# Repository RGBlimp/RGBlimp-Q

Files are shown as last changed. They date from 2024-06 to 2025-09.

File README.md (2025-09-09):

# RGBlimp-Q: Robotic Gliding Blimp With Moving Mass Control Based on a Bird-Inspired Continuum Arm
<div align="center">
    <a href="https://www.youtube.com/watch?v=U8VfF37lHvU" target="_blank">RGBlimp-Q</a>
</div>

These are the hardware and code for RGBlimp-Q. 

* [Project Page](https://RGBlimp.github.io)
* [Paper](https://arxiv.org/abs/2406.10810)
* [Video](https://youtu.be/U8VfF37lHvU)

# Demonstrations
### Robust Flight Against Wind
<div align="center">
    <br/>
    <br/>
    <br/>
</div>

### Attitude Adjustment
<div align="center">
    <br/>
    <br/>
</div>

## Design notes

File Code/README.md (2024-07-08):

# RGBlimp-Q Code

## ESP32-Arduino
ESP32 is a low-cost, low-power system on a chip microcontrollers with integrated Wi-Fi and dual-mode Bluetooth, which could be programmed through Arduino IDE. 

### Installing Arduino-ESP32 Support
Stable release link:
```
https://espressif.github.io/arduino-esp32/package_esp32_index.json
```
To start the installation process using the Boards Manager, follow these steps:
* Install the current upstream Arduino IDE at the 1.8 level or later. The current version is at the arduino.cc website.

* Start Arduino and open the Preferences window.

* Enter one of the release links above into Additional Board Manager URLs field. You can add multiple URLs, separating them with commas.

* Open Boards Manager from Tools > Board menu and install esp32 platform (and do not forget to select your ESP32 board from Tools > Board menu after installation).

* Restart Arduino IDE.

###### * See [Installing Guides](https://docs.espressif.com/projects/arduino-esp32/en/latest/installing.html) for more details on how to install the Arduino ESP32 support. 

### Installing Rosserial Arduino Library
Rosserial is a protocol for wrapping standard ROS serialized messages and multiplexing multiple topics and services over a character device such as a serial port or network socket. 
The rosserial arduino library support for Arduino compatible boards including ESP32. 

To install rosserial arduino library for Arduino IDE, follow these steps:
* Open the **Library Manager** from the IDE menu in Sketch -> Include Library -> Manage Library. 
* Search for "rosserial", and install. 

###### * See [Installing Guides](https://wiki.ros.org/rosserial_arduino/Tutorials/Arduino%20IDE%20Setup) for more details on how to install the rosserial arduino library for Arduino IDE. 

## ROS Package
This ROS package has been tested with ROS Melodic under Ubuntu 18.04. 
```
# Copy rgblimp_ros to catkin workspace

cd ~/catkin_ws/
catkin_make

source ~/catkin_ws/devel/setup.bash

roslaunch rgblimp_ros rgblimp_keyboard.launch
roslaunch rgblimp_ros rgblimp_tuner.launch
```

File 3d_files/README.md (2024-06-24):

# RGBlimp-Q Hardware 3D Files
### These files are derived from *Solidworks 2019 sp0*. 
<div align="center">
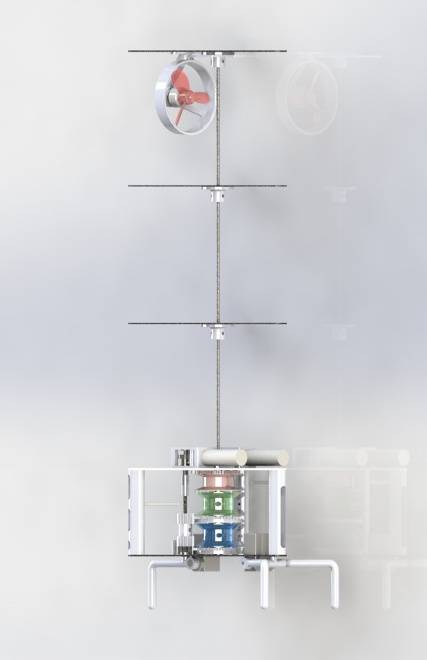
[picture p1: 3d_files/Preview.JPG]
    <br/>
    <sup>CAD Preview</sup><br/><br/>
</div>

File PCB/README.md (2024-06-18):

# RGBlimp-Q PCB

<div align="center">
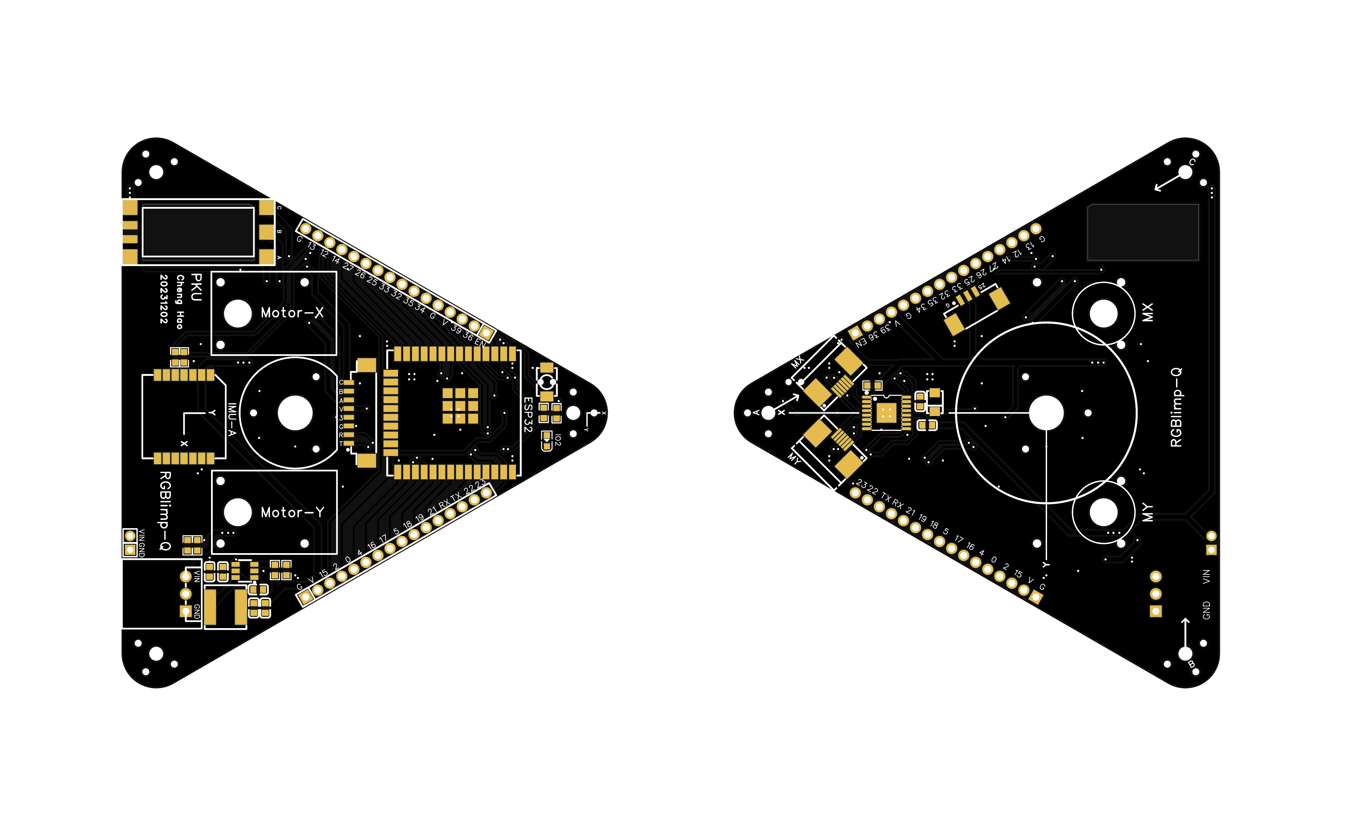
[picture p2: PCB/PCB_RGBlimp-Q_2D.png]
    <br/>
    <sup>Control Unit Circuit Board</sup><br/><br/>
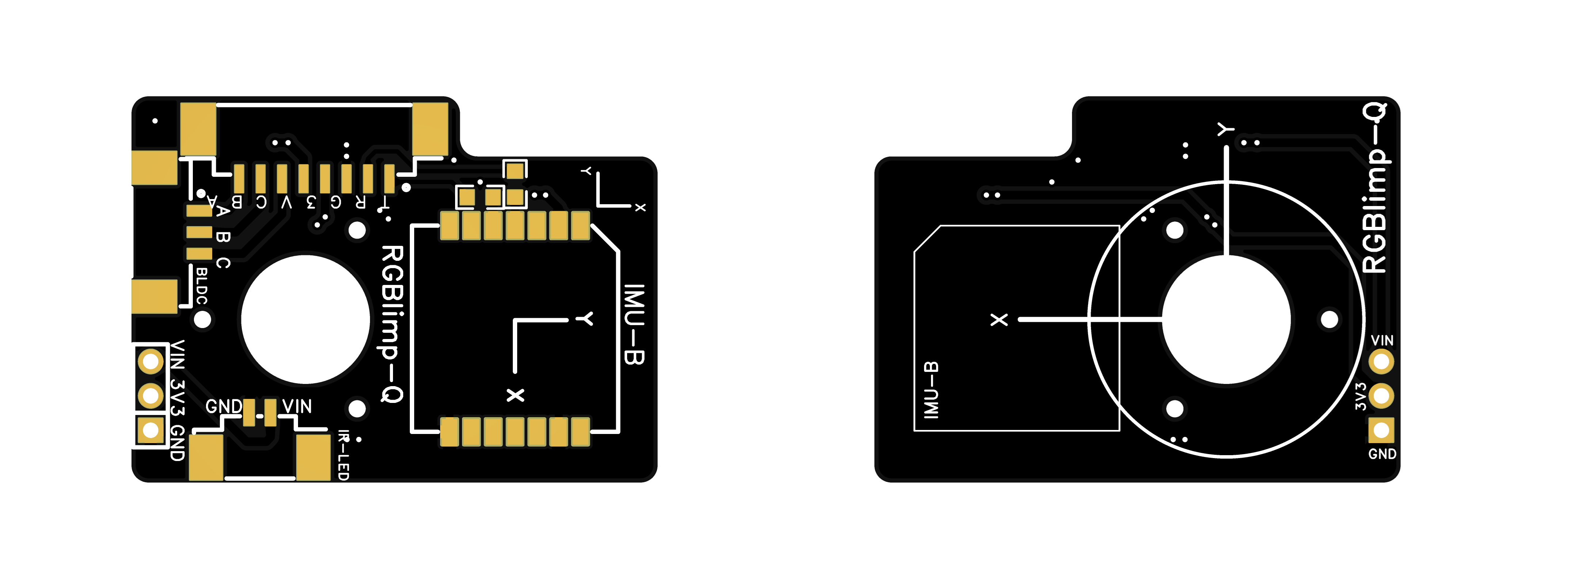
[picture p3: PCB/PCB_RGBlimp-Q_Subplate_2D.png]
    <br/>
    <sup>Subplate Circuit Board</sup>
</div>

## EasyEDA
The PCB project is also open-sourced on
[EasyEDA](https://oshwlab.com/ericccc413/rgblimp-q_)

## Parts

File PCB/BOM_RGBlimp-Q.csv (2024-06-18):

No. | Quantity | Comment | Designator(Main) | Footprint | Value | Manufacturer Part | Manufacturer | Supplier Part | Supplier
1 | 2 | 22uF | C1,C3 | C0603 |  | CL10A226MQ8NRNC | SAMSUNG | C59461 | LCSC
2 | 2 | 100nF | C2,C4 | C0603 |  | CC0603KRX7R9BB104 | YAGEO | C14663 | LCSC
3 | 1 | 22nF | C5 | C0603 |  | 0603B223K500NT | FH | C77571 | LCSC
4 | 1 | 10uF | C6 | CAP-SMD_L3.2-W1.6 |  | CA45-A-16V-10μF-K | TORCH | C185774 | LCSC
5 | 1 | 10nF | C7 | C0603 |  | GRM188R71H103KA01D | muRata | C77053 | LCSC
6 | 1 | 2.2uF | C8 | C0603 |  | CL10A225KO8NNNC | SAMSUNG | C23630 | LCSC
7 | 1 | S3B-XH-A (LF)(SN) | CN0 | CONN-TH_S3B-XH-A-LF-SN-RGBLIMP |  | S3B-XH-A(LF)(SN) | JST | C157928 | LCSC
9 | 1 | AFC12-S08CCC-00 | CN3 | CONN-SMD_8P-P1.25-V-M_AFC12-S08CCC-00 |  | AFC12-S08CCC-00 | JS | C395349 | LCSC
10 | 1 | AFC12-S03CCC-00 | CN4 | CONN-SMD_AFC12-S03CCC-00 |  | AFC12-S03CCC-00 | JS | C395344 | LCSC
11 | 1 | ESP32-WROOM-32UE(16MB) | ESP32 | WIFI-SMD_ESP32-WROOM-32UE |  | ESP32-WROOM-32UE-N16 | ESPRESSIF | C701346 | LCSC
13 | 1 | HI229 | IMU-A | HI229
14 | 1 | 10uH | L1 | IND-SMD_L6.0-W6.0_SWPA6045S |  | SWPA6045S100MT | Sunlord | C79272 | LCSC
15 | 1 | FC-DA1608BK-470H10 | LED1 | LED0603-RD |  | NCD0603B1 |  | C84266 | LCSC
16 | 2 | KH-FG0.5-H2.0-6PIN | MX,MY | FPC-SMD_KH-FG0.5-H2.0-6PIN |  | KH-FG0.5-H2.0-6PIN | Shenzhen Kinghelm Elec | C709363 | LCSC
17 | 1 | 68kΩ | R1 | R0603 |  | 0603WAF6802T5E | UNI-ROYAL | C23231 | LCSC
18 | 1 | 15kΩ | R2 | R0603 |  | 0603WAF1502T5E | UNI-ROYAL | C22809 | LCSC
19 | 2 | 10kΩ | R3,R6 | R0603 |  | 0603WAF1002T5E | UNI-ROYAL | C25804 | LCSC
20 | 1 | 20kΩ | R4 | R0603 |  | 0603WAF2002T5E | UNI-ROYAL | C4184 | LCSC
21 | 1 | 1kΩ | R5 | R0603 |  | 0603WAF1001T5E | UNI-ROYAL | C21190 | LCSC
22 | 1 | 47kΩ | R7 | R0603 |  | 0603WAF4702T5E | UNI-ROYAL | C25819 | LCSC
23 | 2 | 120Ω | R8,R9 | R0603 |  | 0603WAF1200T5E | UNI-ROYAL | C22787 | LCSC
24 | 1 | TSA343G00D-250J2 | SW1 | SW-SMD_L4.0-W2.9-P4.15-EH |  | TSA343G00D-250J2 | BRIGHT | C354947 | LCSC
25 | 1 | DRV8833PWP | U1 | TSSOP-16_L5.0-W4.4-P0.65-LS6.4-BL-EP |  | DRV8833PWPR | TI | C50506 | LCSC
26 | 1 | MT2492 | U2 | SOT-23-6_L2.9-W1.6-P0.95-LS2.8-BR |  | MT2492 | AEROSEMI | C89358 | LCSC
27 | 1 | EMAX_ESC_BULLET_6A | U3 | EMAX_ESC_BULLET_6A
No. | Quantity | Comment | Designator(Subplate) | Footprint | Value | Manufacturer Part | Manufacturer | Supplier Part | Supplier
1 | 1 | AFC12-S08CCC-00 | CN1 | CONN-SMD_8P-P1.25-V-M_AFC12-S08CCC-00-TAOBAO |  | AFC12-S08CCC-00 | JS | C395349 | LCSC
2 | 1 | AFC12-S03CCC-00 | CN2 | CONN-SMD_AFC12-S03CCC-00 |  | AFC12-S03CCC-00 | JS | C395344 | LCSC
5 | 1 | HI229 | IMU-B | HI229
6 | 2 | 120Ω | R1,R2 | R0603 |  | 0603WAF1200T5E | UNI-ROYAL | C22787 | LCSC

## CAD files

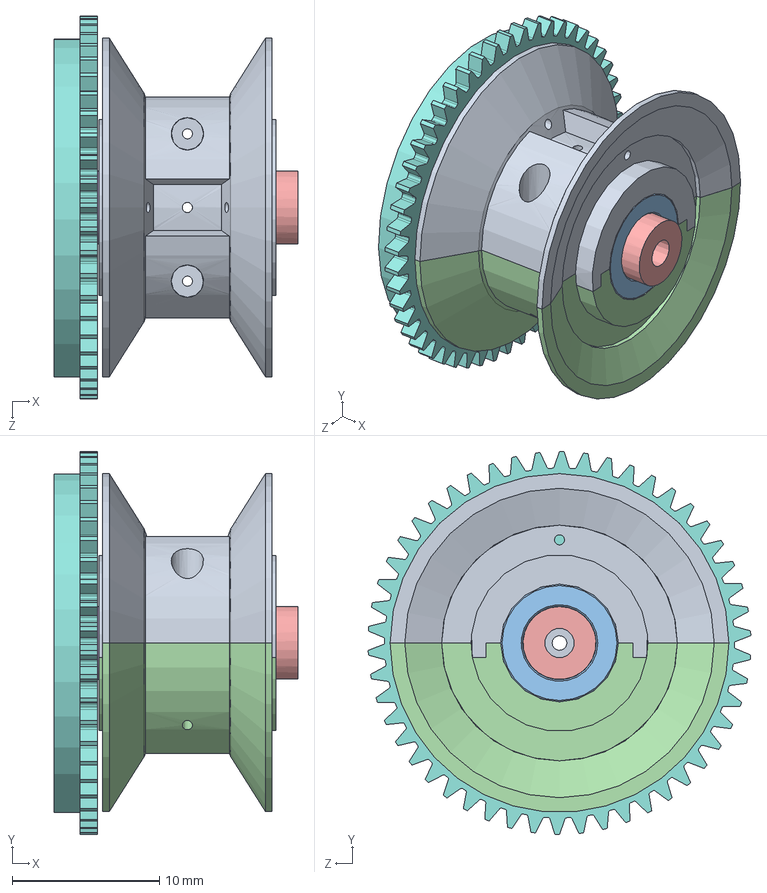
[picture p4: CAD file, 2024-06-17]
3d_files/SLDPRT/_DiffReel.SLDASM
16.6 x 26.0 x 26.0 mm
DifferReelA
Bearing_3-1-1 x 2
Bearing_8-5-2.5 x 2
DifferReelB
GearA1
GearA2
GearA3 x 2
wheelB3
Bearing_PTFE

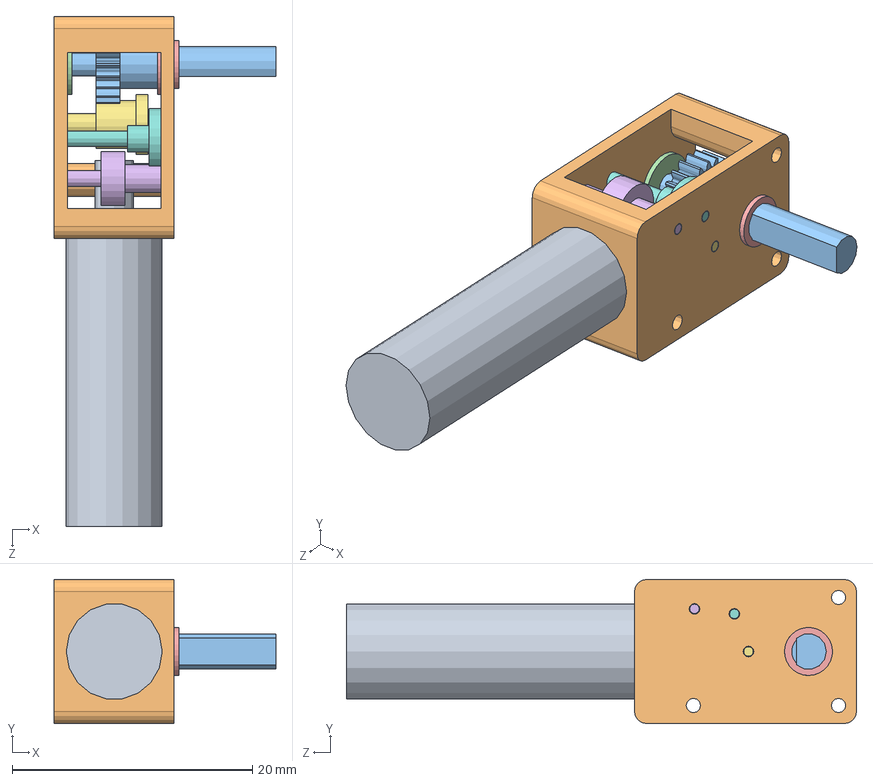
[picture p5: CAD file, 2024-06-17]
3d_files/SLDPRT/_Motor2.SLDASM
18.5 x 12.0 x 42.5 mm
Motor
MotorGearBox
MotorGear1
MotorBear2
MotorBear
MotorGear4
MotorGear2
MotorGear3

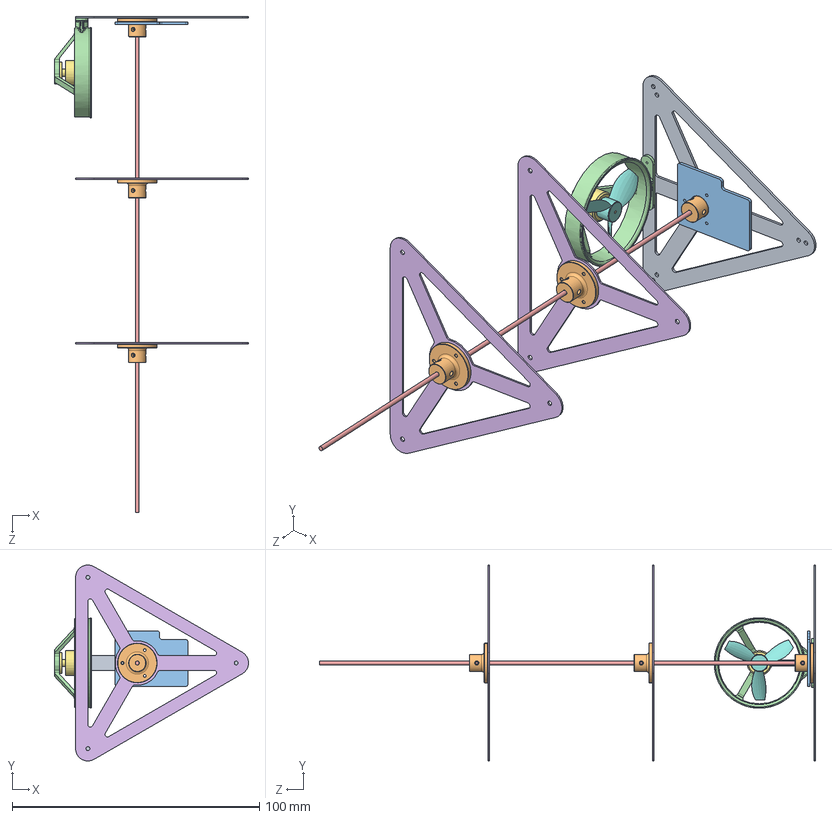
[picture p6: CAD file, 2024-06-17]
3d_files/SLDPRT/_ContinuumBody.SLDASM
78.5 x 79.3 x 200.8 mm
Frame1
Seat1 x 3
FrameSub(PCB)
ThrusterHolder
Backbone
Frame2 x 2
BLDC
Propeller

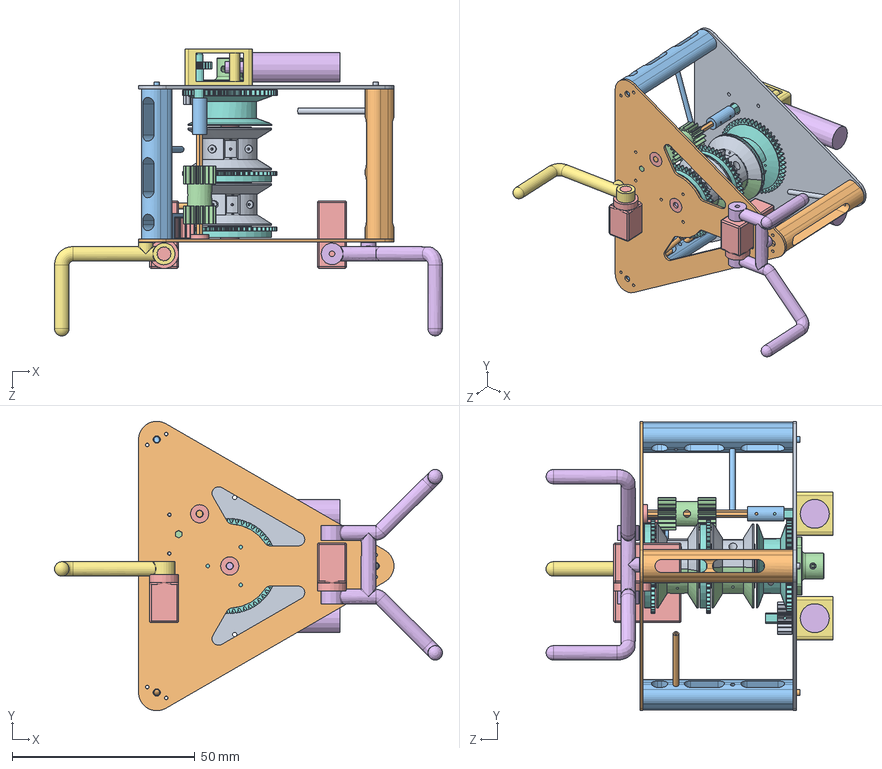
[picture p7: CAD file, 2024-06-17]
3d_files/SLDPRT/_DrivingUnit.SLDASM
106.3 x 79.3 x 78.6 mm
Frame3(PCB)
Pillar1
Pillar2 x 2
Seat2
Bearing_5-2-2 x 3
Axis1
Gasket x 5
FixedAxisReel
DifferReelA x 2
Bearing_3-1-1 x 4
Bearing_8-5-2.5 x 4
DifferReelB x 2
GearA1 x 2
GearA2 x 2
GearA3 x 4
wheelB3 x 2
Bearing_PTFE x 2
Frame4
Holder
Axis3
GearB3
Motor x 2
MotorGearBox x 2
MotorGear1 x 2
GearB1
Axis2
Coupler
GearB2
Servo x 2
ClawA
ClawB
Bearing_PTFE2
Pipe1
Pipe2
Pipe3

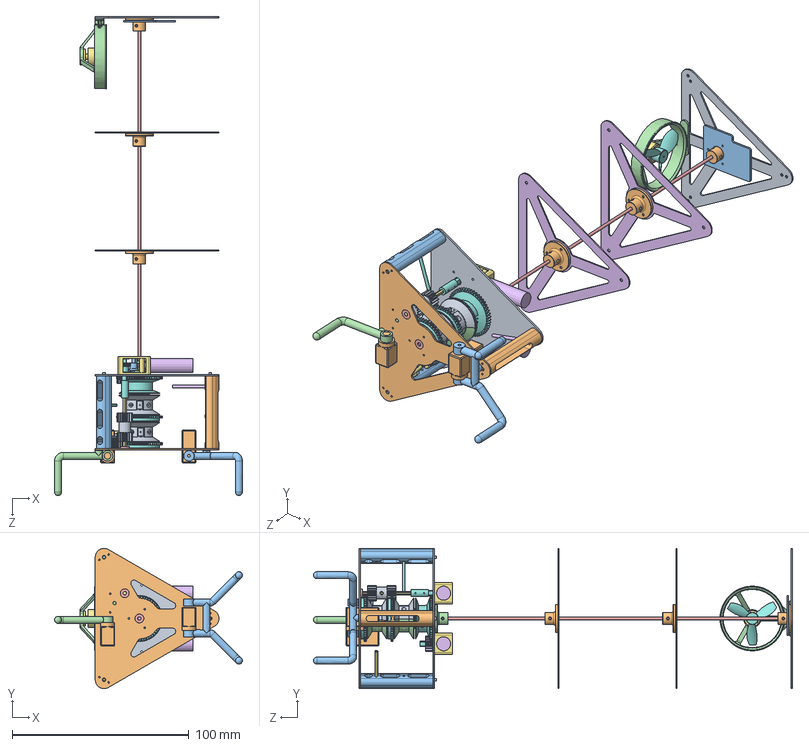
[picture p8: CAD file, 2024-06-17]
3d_files/SLDPRT/_ConintuumArm.SLDASM
106.3 x 79.3 x 270.9 mm
Frame1
Seat1 x 3
FrameSub(PCB)
ThrusterHolder
Backbone
Frame2 x 2
BLDC
Propeller
Frame3(PCB)
Pillar1
Pillar2 x 2
Seat2
Bearing_5-2-2 x 3
Axis1
Gasket x 5
FixedAxisReel
DifferReelA x 2
Bearing_3-1-1 x 4
Bearing_8-5-2.5 x 4
DifferReelB x 2
GearA1 x 2
GearA2 x 2
GearA3 x 4
wheelB3 x 2
Bearing_PTFE x 2
Frame4
Holder
Axis3
GearB3
Motor x 2
MotorGearBox x 2
MotorGear1 x 2
MotorBear x 2
MotorBear2 x 2
MotorGear2 x 2
MotorGear3 x 2
MotorGear4 x 2
GearB1
Axis2
Coupler
GearB2
Servo x 2
ClawA
ClawB
Bearing_PTFE2
Pipe1
Pipe2
Pipe3

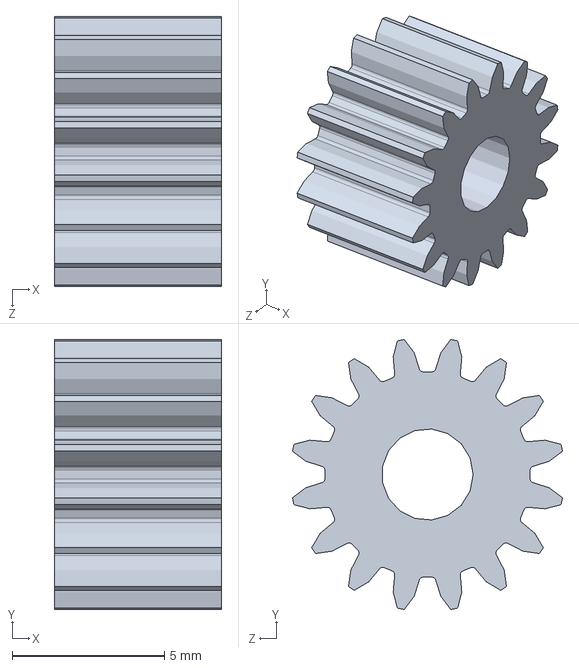
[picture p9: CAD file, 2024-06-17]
3d_files/SLDPRT/GearB3.SLDPRT
5.50 x 8.87 x 8.87 mm

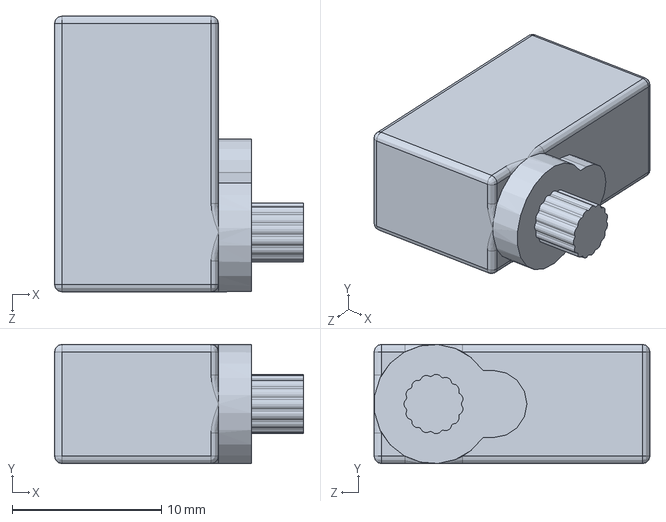
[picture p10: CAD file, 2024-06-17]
3d_files/SLDPRT/Servo.SLDPRT
16.7 x 8.00 x 18.5 mm

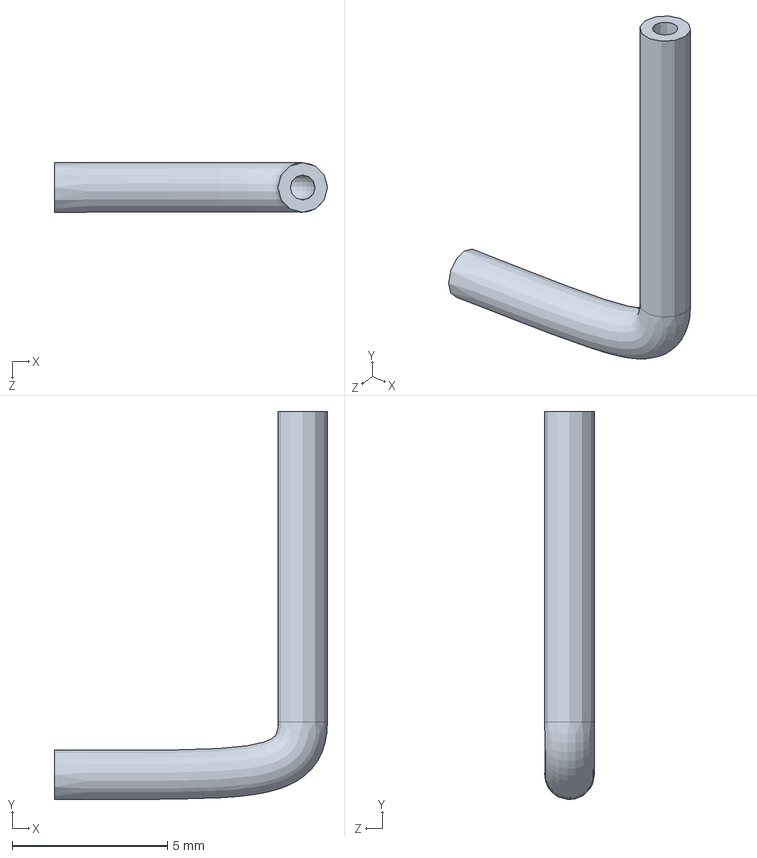
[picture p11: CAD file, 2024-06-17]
3d_files/SLDPRT/Pipe2.SLDPRT
8.80 x 12.5 x 1.60 mm

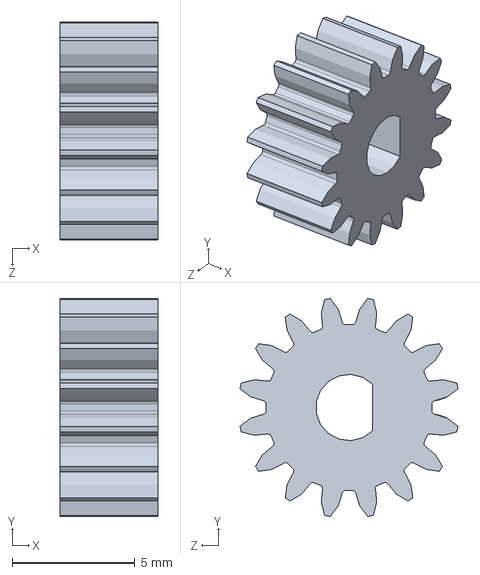
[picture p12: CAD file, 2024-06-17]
3d_files/SLDPRT/GearB1.SLDPRT
4.00 x 8.87 x 8.87 mm

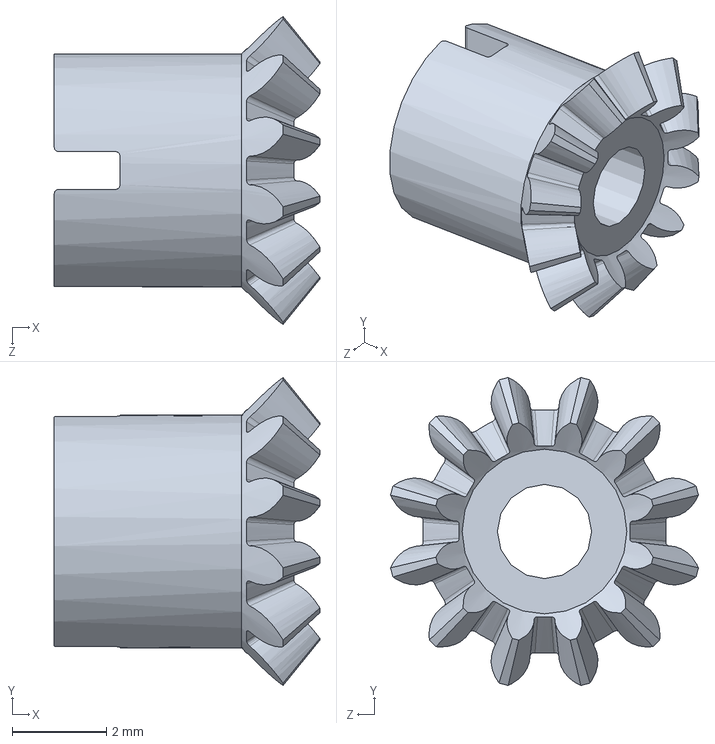
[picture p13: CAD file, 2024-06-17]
3d_files/SLDPRT/GearA2.SLDPRT
5.63 x 6.53 x 6.53 mm

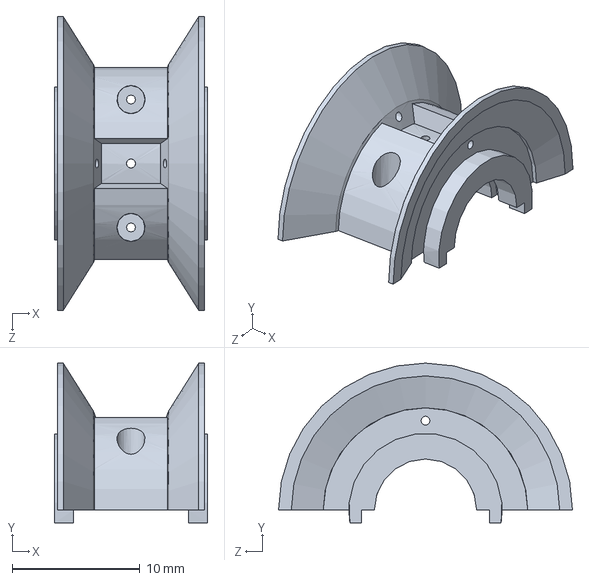
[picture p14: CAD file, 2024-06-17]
3d_files/SLDPRT/DifferReelA.SLDPRT
12.0 x 12.5 x 23.0 mm

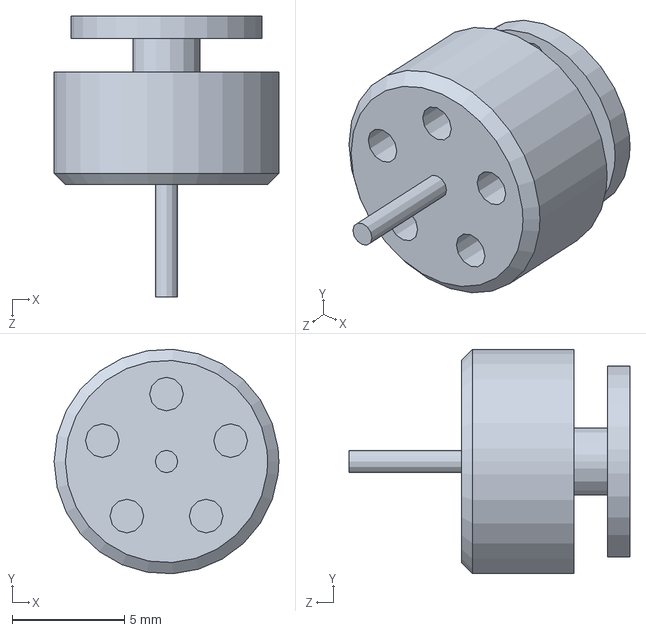
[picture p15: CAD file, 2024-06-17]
3d_files/SLDPRT/BLDC.SLDPRT
10.0 x 9.98 x 12.5 mm

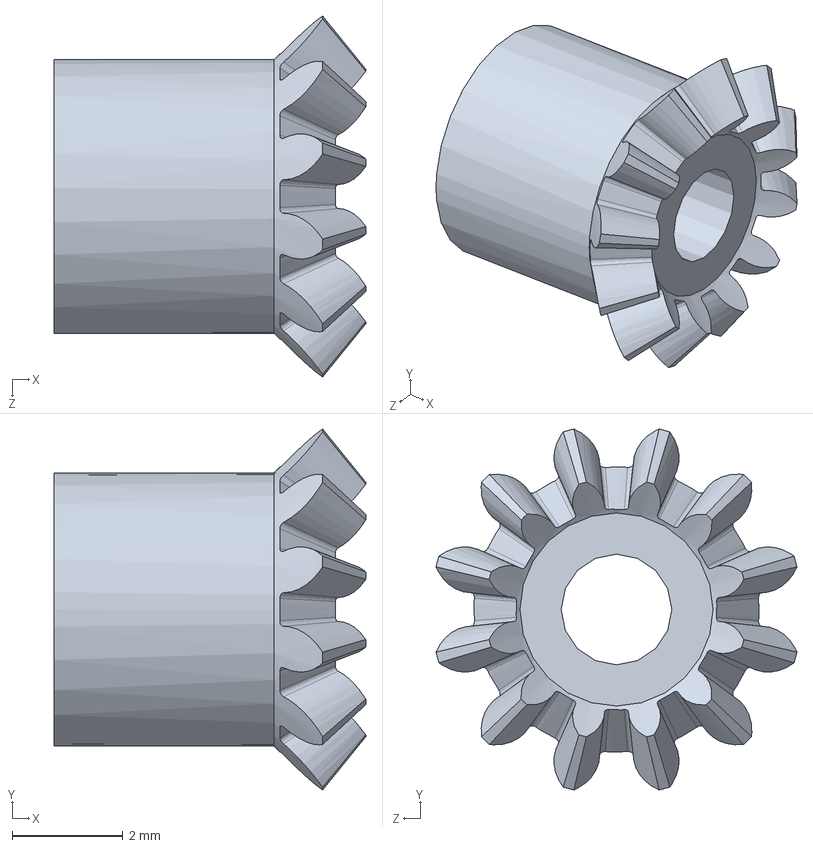
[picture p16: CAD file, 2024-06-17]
3d_files/SLDPRT/GearA1.SLDPRT
5.63 x 6.53 x 6.53 mm

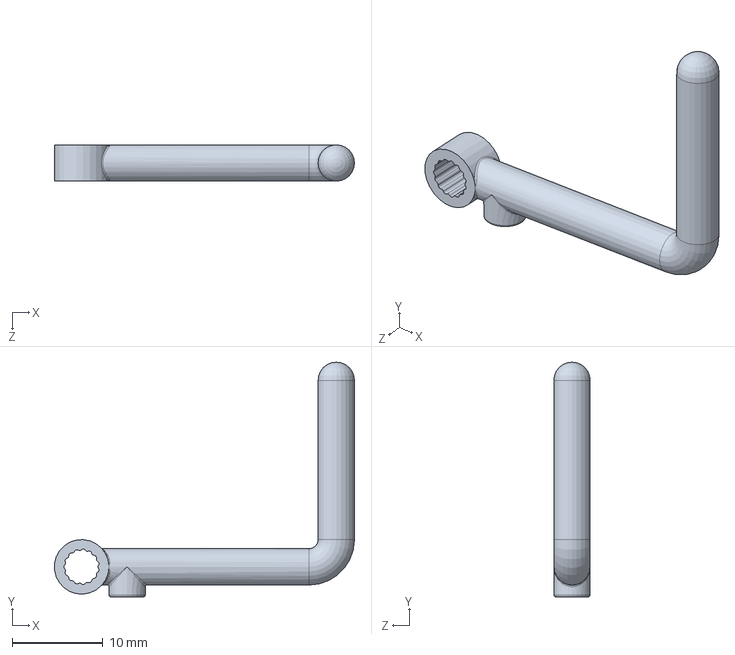
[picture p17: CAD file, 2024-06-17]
3d_files/SLDPRT/ClawB.SLDPRT
33.0 x 25.8 x 4.00 mm

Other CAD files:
3d_files/SLDPRT/_Motor1.SLDASM
3d_files/SLDPRT/Frame3(PCB).SLDPRT
3d_files/SLDPRT/Holder.SLDPRT
3d_files/SLDPRT/Pillar2.SLDPRT
3d_files/SLDPRT/Axis1.SLDPRT
3d_files/SLDPRT/Axis2.SLDPRT
3d_files/SLDPRT/Axis3.SLDPRT
3d_files/SLDPRT/Backbone.SLDPRT
3d_files/SLDPRT/Bearing_3-1-1.SLDPRT
3d_files/SLDPRT/Bearing_5-2-2.SLDPRT
3d_files/SLDPRT/Bearing_8-5-2.5.SLDPRT
3d_files/SLDPRT/Bearing_PTFE.SLDPRT
3d_files/SLDPRT/Bearing_PTFE2.SLDPRT
3d_files/SLDPRT/ClawA.SLDPRT
3d_files/SLDPRT/Coupler.SLDPRT
3d_files/SLDPRT/DifferReelB.SLDPRT
3d_files/SLDPRT/FixedAxisReel.SLDPRT
3d_files/SLDPRT/Frame1.SLDPRT
3d_files/SLDPRT/Frame2.SLDPRT
3d_files/SLDPRT/Frame4.SLDPRT
3d_files/SLDPRT/FrameSub(PCB).SLDPRT
3d_files/SLDPRT/Gasket.SLDPRT
3d_files/SLDPRT/GearA3.SLDPRT
3d_files/SLDPRT/GearB2.SLDPRT
3d_files/SLDPRT/Motor.SLDPRT
3d_files/SLDPRT/MotorBear.SLDPRT
3d_files/SLDPRT/MotorBear2.SLDPRT
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

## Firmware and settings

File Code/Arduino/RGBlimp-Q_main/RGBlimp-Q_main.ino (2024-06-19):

// RGBlimp-Q Main Controller
// Last Edit: 2024-6-19

#include <soc/soc.h>
#include <soc/rtc_cntl_reg.h>
#include <WiFi.h>
#include <ros.h>
#include <std_msgs/UInt64.h>
#include <geometry_msgs/Quaternion.h>
#include <geometry_msgs/Point.h>
#include <sensor_msgs/Imu.h>
#include <string.h>
#include <math.h>
#include <EEPROM.h>

#define MIN(i, j) (((i) < (j)) ? (i) : (j))
#define MAX(i, j) (((i) > (j)) ? (i) : (j))

#define LED_BUILTIN 2
#define THRUST 27
#define GDLX_A 32
#define GDLX_B 33
#define GDLY_A 22
#define GDLY_B 23
#define IMUA_T 13
#define IMUA_R 14
#define IMUB_T 16
#define IMUB_R 17
#define GRIPPER 25

#define THRUST_MAX 300

#define GD_CLS  0x0
#define GD_X    0x1
#define GD_Y    0x2
#define GD_XY   0x3

#define FB_GD   0x0  // Gondola Distance Feedback Control
#define FB_SF   0x1  // Straight Feedback Flight     (Yaw Adjustment)
#define FB_ES   0x2  // Eular Spiral Flight (Following a Ramp Signal)
#define FB_SQ   0x3  // Square End Motion Trajectory of the Continuum Arm   (Following a piecewise function composed of different trigonometric functions)
#define FB_TR   0x4  // Triangular End Motion Trajectory of the Continuum Arm   (Following a piecewise function composed of different trigonometric functions)



// IMU
unsigned char buffer[40];
sensor_msgs::Imu IMU;
geometry_msgs::Quaternion IMUA,IMUB,q;
float psi = 0.0, psi_ = 0.0; // Yaw & Ratio of Body Frame 
float phiA=0,thetaA=0,phiB=0,thetaB=0;

// Parameters
std_msgs::UInt64 params; // params = deltaX + deltaY*2^8

// Calibration
float deltaX = 0.0, deltaY = 0.0;

// Feedback Control
ushort isGD = 0;  // Gondola Distance Mode  (GD_CLS,GD_X,GD_Y,GD_XY)
ushort fbCN = 0;  // Gondola Feedback Control Mode Number
struct pid{
  float target;
  float measure;
  float err;
  float err_last;
  float Kp,Ki,Kd;
  float integral;
} Gx,Gy,sf; 
float stMax = 0.0;
float slope = 0.0;  // [mm/s] The slope of target function for Eular Spiral (fbCN=2)
float AxLemn=0.0, AyLemn=0.0, taLemn = 0.0, tbLemn = 0.0;  // [mm,ms]  The amplitude and period time for Lemniscate (fbCN=3)
bool loopLemn=0;
uint32_t startTime = 0, cntLemn = 0;


// Wi-Fi
const char* ssid     = "RGBlimp";
const char* password = "robot2021";

// ROS SETUP
IPAddress server(192,168,0,101); //ros server IP ros master
const uint16_t serverPort = 11411; 
ros::NodeHandle nh;


uint16_t crc16(unsigned char *addr, int num, uint16_t crc){
 ushort i;
  for (; num > 0; num--){           /* Step through bytes in memory */
    crc = crc ^ (*addr++ << 8);     /* Fetch byte from memory, XOR into CRC top byte*/
    for (i = 0; i < 8; i++){        /* Prepare to rotate 8 bits */
     if (crc & 0x8000)              /* b15 is set... */
      crc = (crc << 1) ^ 0x1021;    /* rotate and XOR with polynomic */
     else                           /* b15 is clear... */
      crc <<= 1;                    /* just rotate */
    }                               /* Loop for 8 bits */
    crc &= 0xFFFF;                  /* Ensure CRC remains 16-bit value */
  }                                 /* Loop until num=0 */
  return(crc);                      /* Return updated CRC */
}


ros::Subscriber<std_msgs::UInt64> sub("/command", &control);
ros::Publisher imu("IMU",&IMU);
ros::Publisher imua("IMUA",&IMUA);
ros::Publisher imub("IMUB",&IMUB);
ros::Publisher param("param",&params);
// CONTROL FUNCTION  "/command"
void control(const std_msgs::UInt64 &msg){  
  // msg.data = A + B*2^10 + C*2^20 + D*2^30 + E*2^40 + F*2^50 + SIGN*2^60
  uint16_t A =  msg.data%1024;      // in [0,2^10) = [0,1024)
  uint16_t B = (msg.data>>10)%1024; // in [0,2^10) = [0,1024)
  uint16_t C = (msg.data>>20)%1024; // in [0,2^10) = [0,1024)
  uint16_t D = (msg.data>>30)%1024; // in [0,2^10) = [0,1024)
  uint16_t E = (msg.data>>40)%1024; // in [0,2^10) = [0,1024)
  uint16_t F = (msg.data>>50)%1024; // in [0,2^10) = [0,1024)
  uint16_t S =  msg.data>>60;       // in [0,2^4)  = [0,16)
  if(S==0){thrust(0);              // [0] Emergency Stop
           gondola(500,500);
           fbCN=FB_GD;isGD=GD_CLS;}
  if(S==1) thrust(A);               // [1] Thrust             (A)      A>>[0,500]
  if(S==2) gripper(A);              // [2] Gripper            (A)      A>>[0,90] deg
  if(S==3){fbCN=FB_GD;isGD=GD_CLS;  // [3] Gondola Throttle   (A,B)    A,B>>[0,1000]->[-500,500]
           gondola(A,B);}
  if(S==4) fbCtrl(A,B,C,D,E,F);     // [4] Gondola Feedback   (A,B,C,D,E,F)   F:(0 FB_GD, 1 FB_SF, 2 FB_ES, 3 FB_SQ)
  if(S==9){if(!A)calib();           // [9] Calibrate the deviation of the Gondola origin
           else{EEPROM.write(0, uint8_t(A));  // [0,255]->[0,240]->[-120,120]->[-3.0:0.025:3.0] uint8_t(()*40 + 120)  [-1.35,2.00]
                EEPROM.write(1, uint8_t(B));
                EEPROM.commit();
                deltaX = (float(EEPROM.read(0))-120)/40;
                deltaY = (float(EEPROM.read(1))-120)/40;
                digitalWrite(LED_BUILTIN,LOW);delay(200); 
                digitalWrite(LED_BUILTIN,HIGH);}}
  if(S==10)param.publish(&params);
}


void calib(){
  deltaX = 0;
  deltaY = 0;
  for(int i=0; i<1000; i++,delay(5)){
    gondola( thetaB*(800)+500, phiB*(-800)+500 );
    //Serial.printf("[thetaB,phiB]=[%.3f,%.3f]\n",thetaB,phiB);
  }
  gondola( 500, 500);
  EEPROM.write(0, uint8_t((MAX(-2.0,MIN(2.0, Gx.measure )))*40 + 120) );  // [0,255]->[0,240]->[-120,120]->[-3.0:0.025:3.0]
  EEPROM.write(1, uint8_t((MAX(-2.0,MIN(2.0, Gy.measure )))*40 + 120) );
  EEPROM.commit();
  deltaX = (float(EEPROM.read(0))-120)/40;
  deltaY = (float(EEPROM.read(1))-120)/40;
  //Serial.printf("Calib.[x,y]=[%.3f,%.3f],   G.[x,y]=[%.3f,%.3f]\n",deltaX,deltaY,(MAX(-2.0,MIN(2.0, Gx.measure )))*40 + 120,(MAX(-2.0,MIN(2.0, Gy.measure )))*40 + 120);
  params.data = EEPROM.read(0) + EEPROM.read(1)*256;
  digitalWrite(LED_BUILTIN,LOW);
  delay(200); 
  digitalWrite(LED_BUILTIN,HIGH);
}

// THRUST  (A)    A>>[0,500]
void thrust(uint16_t T){
  T = T>THRUST_MAX?THRUST_MAX:T; 
  ledcWrite(0, 520+T); 
}

// GONDOLA Throttle (A,B)  A,B>>[0,1000]  ->  [-500,500]
void gondola(uint16_t x, uint16_t y){
  int xx = (x>1000?1000:x) - 500; 
  int yy = (y>1000?1000:y) - 500; 
  // x-o-z Plane
  if (xx>0){
    ledcWrite(8, 0);
    ledcWrite(9,  int(xx*2.046));    // MX FORWARD
    }
  else {
    ledcWrite(8, -int(xx*2.046));    // MX BACKWARD
    ledcWrite(9, 0);
    }
  // y-o-z Plane
  if (yy>0){
    ledcWrite(10, 0);
    ledcWrite(11,  int(yy*2.046));   // MY FORWARD
    }
  else {
    ledcWrite(10, -int(yy*2.046));   // MY BACKWARD
    ledcWrite(11, 0);
    }
}

// GRIPPER  (A)    A>>[0,90]
void gripper(uint16_t d){
  d = d>90?90:d; 
  ledcWrite(12, 51+int(d*0.56666)); 
}

// Feedback Control
void fbCtrl(uint16_t A, uint16_t B, uint16_t C, uint16_t D, uint16_t E, uint16_t F){
  if (F==0){ // Gondola Distance(xy) Feedback Control
    Gx.integral=0.0, Gy.integral=0.0;
    Gx.target=((A-500.0)/8.0);  // A [0,1000] -> [-62.5,62.5] [mm]
    Gy.target=((B-500.0)/8.0);  // B [0,1000] -> [-62.5,62.5] [mm]
    Gx.Kp=C?C:50.0;             // C [0,1000]
    Gy.Kp=C?C:50.0;         
    Gx.Ki=D?(D/10):0.10;        // D [0,1000] -> [0.0,100.0]
    Gy.Ki=D?(D/10):0.10;
    Gx.Kd=E?(E/10):0.10;        // E [0,1000] -> [0.0,100.0]
    Gy.Kd=E?(E/10):0.10;
    fbCN = FB_GD; 
    isGD = GD_XY; 
  }
  if (F==1){ // Straight Flight Feedback Control
    // Set the yaw angle in this time as straight flight direction
    sf.target=psi;              // [deg]
    sf.Kp=A;//?A:50;            // A [0,1000]
    sf.Kd=B;//?(B/10):0.10;     // B [0,1000] -> [0.0,100.0]
    stMax=C?MIN(45,C):20;       // C [0,40]
    fbCN = FB_SF; 
    isGD = GD_Y; 
  }
  if (F==2){ // Gy.target = A*t + B
    // Following a ramp signal
    Gy.integral=0.0;
    Gy.target=B;                // B [0,1000]
    slope=(A-500)/8.0;          // A [0,1000] -> [-62.5,62.5] [mm]
    fbCN = FB_ES; 
    isGD = GD_Y; 
  }
  if (F==3){ // Square End Motion Trajectory
    AxLemn=A;              //[mm] A [0,1000]
    AyLemn=B;              //[mm] B [0,1000] 
    taLemn=C?C*100:10000;       //[ms] C [0,1000] -> [0.0,100.0] [s] -> [0.0, 100000] [ms]
    tbLemn=D?D*100:10000;       //[ms] D [0,1000] -> [0.0,100.0] [s] -> [0.0, 100000] [ms]
    loopLemn=E?1:0;
    startTime = esp_log_timestamp();
    cntLemn = 0;
    fbCN = FB_SQ;
    isGD = (AxLemn<1)?GD_Y:GD_XY;
  }
  if (F==4){ // Triangular End Motion Trajectory 
    AxLemn=A;              //[mm] A [0,1000]
    AyLemn=B;              //[mm] B [0,1000] 
    taLemn=C?C*100:10000;       //[ms] C [0,1000] -> [0.0,100.0] [s] -> [0.0, 100000] [ms]
    tbLemn=D?D*100:10000;       //[ms] D [0,1000] -> [0.0,100.0] [s] -> [0.0, 100000] [ms]
    loopLemn=E?1:0;
    startTime = esp_log_timestamp();
    cntLemn = 0;
    fbCN = FB_TR;
    isGD = (AxLemn<1)?GD_Y:GD_XY;
  }
}

void setup() { 
  WRITE_PERI_REG(RTC_CNTL_BROWN_OUT_REG, 0);  // Close the low-voltage detecter to avoid reboot
  xTaskCreatePinnedToCore(imuUpdate_, "imuUpdate", 10000, NULL, 1, NULL,  1);  //  IMU Update Process   PRO_CPU -- 0 | APP_CPU -- 1
  xTaskCreatePinnedToCore(   fbCtrl_,    "fbCtrl", 10000, NULL, 1, NULL,  1);  //  fbCtrl Process
  
  // Debug
  Serial.begin(115200); 

  // Calibration
  EEPROM.begin(2);
  deltaX = (float(EEPROM.read(0))-120)/40;
  deltaY = (float(EEPROM.read(1))-120)/40;
  Serial.printf("Calib.[x,y]=[%.3f,%.3f]mm\n",deltaX,deltaY);
  params.data = EEPROM.read(0) + EEPROM.read(1)*256;

  // Initialize Thrust PWM
  // freq   1000/125 = 8ms
  // rang   [0,4095] -> [0,8ms]
  // [1ms,2ms]  ->  [4096*1/8,4096*2/8]=[512,1024] -> [520,1020]
  ledcSetup(0, 125, 12); // channel, freq, resolution 
  ledcAttachPin(THRUST, 0); // Pin, channel
  ledcWrite(0, 0); 

  // Initialize Gondola PWM
  ledcSetup(8, 50, 10); // channel, freq, resolution
  ledcSetup(9, 50, 10); // channel, freq, resolution
  ledcSetup(10, 50, 10); // channel, freq, resolution
  ledcSetup(11, 50, 10); // channel, freq, resolution
  ledcAttachPin(GDLX_A, 8); // Pin, channel
  ledcAttachPin(GDLX_B, 9); // Pin, channel
  ledcAttachPin(GDLY_A, 10); // Pin, channel
  ledcAttachPin(GDLY_B, 11); // Pin, channel
  ledcWrite(8, 0); 
  ledcWrite(9, 0);
  ledcWrite(10, 0);
  ledcWrite(11, 0);

  // Initialize Gripper PWM
  // [1ms,2ms]  ->  [1024*1/20,1024*2/20]=[51.2,102.4] -> [51,102]
  ledcSetup(12, 50, 10); // channel, freq, resolution 
  ledcAttachPin(GRIPPER, 12); // Pin, channel
  ledcWrite(12, 51); 

  
  // Initialize the LED
  pinMode(LED_BUILTIN,OUTPUT);
  digitalWrite(LED_BUILTIN,LOW); // Close the LED
  // WiFi Connecting
  WiFi.begin(ssid, password);
  while (WiFi.status() != WL_CONNECTED) { delay(300); digitalWrite(LED_BUILTIN,HIGH);delay(200); digitalWrite(LED_BUILTIN,LOW);}
  digitalWrite(LED_BUILTIN,HIGH); // Open the LED when WiFi connected
  // Rosserial Socket Connecting
  nh.getHardware()->setConnection(server, serverPort);
  nh.initNode();
  nh.subscribe(sub); // Ctrl
  nh.advertise(imu); // IMU full data of Based Frame
  nh.advertise(imua); // IMUA Tool  Frame
  nh.advertise(imub); // IMUB Based Frame
  nh.advertise(param); // Param

  // Initialize IMUs
  Serial1.begin(115200, SERIAL_8N1, IMUA_T, IMUA_R);
  Serial2.begin(115200, SERIAL_8N1, IMUB_T, IMUB_R);
  Serial1.write("AT+SETPTL=D1\r\n", 14);
  Serial2.write("AT+SETPTL=A0,B0,D1\r\n", 20);
  Serial1.write("AT+MODE=0\r\n", 11);  // 0 -- 6 axis; 1 -- 9 axis
  Serial2.write("AT+MODE=0\r\n", 11);  // 
  
  Serial1.write("AT+ODR=50\r\n", 11);  // 50 Hz
  Serial2.write("AT+ODR=50\r\n", 11);  // 50 Hz

  q.w = 1; q.x = 0; q.y = 0; q.z = 0;
  IMUA = q; IMUB = q;
  
  
  // Initialize Thruster BLDC
  /*ledcWrite(0, 1020); 
  delay(3000);*/
  ledcWrite(0, 520); 
}

void loop(){
  nh.spinOnce();
  delay(5);
}


// IMU UPDATE
void imuUpdate_(void *pvParameters) {
  uint16_t crc = 0;
  geometry_msgs::Quaternion tmp, tmpA, tmpB;
  while (1) {
    vTaskDelay(10);
    // IMUB -- Body Frame
    if (Serial2.available() > 0) {
      crc = 0;
      Serial2.readBytes(buffer, 37);
      while (Serial2.read() >= 0);  // Clear the buffer
      if ((buffer[0] << 8) + buffer[1] == 0x5AA5) {
        crc = crc16(buffer, 4, crc);
        crc = crc16(buffer + 6, buffer[2] + (buffer[3] << 8), crc);
        if (crc == (buffer[5] << 8) + buffer[4]) {
          // BUFFER: 
          //   [6]  A0, [7-8]   X, [9-10]  Y, [11-12] Z, 
          //   [13] B0, [14-15] X, [16-17] Y, [18-19] Z, 
          //   [20] D1, [21-24] w, [25,28] x, [29,32] y, [33,36] z
          int16_t tmpimu;
          memcpy(&tmpimu, &buffer[7], sizeof(int16_t));
          IMU.linear_acceleration.y = float(tmpimu)/1000; // [m/s^2]
          memcpy(&tmpimu, &buffer[9], sizeof(int16_t));
          IMU.linear_acceleration.x =-float(tmpimu)/1000; // [m/s^2]
          memcpy(&tmpimu, &buffer[11], sizeof(int16_t));
          IMU.linear_acceleration.z =-float(tmpimu)/1000; // [m/s^2]
          memcpy(&tmpimu, &buffer[14], sizeof(int16_t));
          IMU.angular_velocity.y =-float(tmpimu)/10;      // [deg/s]
          memcpy(&tmpimu, &buffer[16], sizeof(int16_t));
          IMU.angular_velocity.x = float(tmpimu)/10;      // [deg/s]
          memcpy(&tmpimu, &buffer[18], sizeof(int16_t));
          IMU.angular_velocity.z = float(tmpimu)/10;      // [deg/s]
          memcpy(&tmp.w, &buffer[21], sizeof(float));
          memcpy(&tmp.x, &buffer[25], sizeof(float));
          memcpy(&tmp.y, &buffer[29], sizeof(float));
          memcpy(&tmp.z, &buffer[33], sizeof(float));
          IMUB.w = 1 / sqrt(2) * (tmp.x + tmp.y);
          IMUB.x = 1 / sqrt(2) * (tmp.z - tmp.w);
          IMUB.y = 1 / sqrt(2) * (tmp.z + tmp.w);
          IMUB.z = 1 / sqrt(2) * (tmp.x - tmp.y);
          psi  =  atan2(2*(IMUB.w*IMUB.z+IMUB.x*IMUB.y), 1-2*(IMUB.y*IMUB.y+IMUB.z*IMUB.z))*180/3.14; // deg
          psi_ =-IMU.angular_velocity.z;  // [deg/s]  note: following the legacy code
          //Serial.printf("IMUB.[w,x,y,z]=[%.3f,%.3f,%.3f,%.3f], [psi,psi_]=[%.3f,%.3f]\n",IMUB.w,IMUB.x,IMUB.y,IMUB.z,psi,psi_);
          IMU.header.stamp = nh.now();
          IMU.orientation = IMUB;
          imub.publish(&IMUB);
          imu.publish(&IMU);
        }
      }
    }

    // IMUA & q -- Tool Frame
    if (Serial1.available() > 0) {
      crc = 0;
      Serial1.readBytes(buffer, 23);
      while (Serial1.read() >= 0);  // Clear the buffer
      if ((buffer[0] << 8) + buffer[1] == 0x5AA5) {
        crc = crc16(buffer, 4, crc);
        crc = crc16(buffer + 6, buffer[2] + (buffer[3] << 8), crc);
        if (crc == (buffer[5] << 8) + buffer[4]) {
          // BUFFER: [6] D1, [7-10] w, [11,14] x, [15,18] y, [19,22] z
          memcpy(&tmp.w, &buffer[7], sizeof(float));
          memcpy(&tmp.x, &buffer[11], sizeof(float));
          memcpy(&tmp.y, &buffer[15], sizeof(float));
          memcpy(&tmp.z, &buffer[19], sizeof(float));
          IMUA.w = 1 / sqrt(2) * (tmp.z - tmp.w);
          IMUA.x =-1 / sqrt(2) * (tmp.y + tmp.x);
          IMUA.y = 1 / sqrt(2) * (tmp.y - tmp.x);
          IMUA.z = 1 / sqrt(2) * (tmp.z + tmp.w);
          phiA = atan2(2 * (IMUA.w * IMUA.x + IMUA.y * IMUA.z), 1 - 2 * (IMUA.x * IMUA.x + IMUA.y * IMUA.y));
          thetaA = asin(2 * (IMUA.w * IMUA.y - IMUA.x * IMUA.z));
          //Serial.printf("IMUA.[w,x,y,z]=[%.3f,%.3f,%.3f,%.3f]\n",IMUA.w,IMUA.x,IMUA.y,IMUA.z);
          //Serial.printf("IMUA.[Phi,Theta,Psi]=[%.3f,%.3f,%.3f]\n", phiA*180/3.14, thetaA*180/3.14, atan2(2*(IMUA.w*IMUA.z+IMUA.x*IMUA.y), 1-2*(IMUA.y*IMUA.y+IMUA.z*IMUA.z))*180/3.14);
          
          // Compute the Configuration of Continuum Arm
          // 1. Set the yaw of the IMUB as 0
          phiB = atan2(2 * (IMUB.w * IMUB.x + IMUB.y * IMUB.z), 1 - 2 * (IMUB.x * IMUB.x + IMUB.y * IMUB.y));
          thetaB = asin(2 * (IMUB.w * IMUB.y - IMUB.x * IMUB.z));
          //Serial.printf("IMUB.[Phi,Theta,Psi]=[%.3f,%.3f,%.3f]\n",phiB*180/3.14,thetaB*180/3.14,psi);
          tmpA.w = cos(phiA / 2) * cos(thetaA / 2);  // Modified IMUA data
          tmpA.x = sin(phiA / 2) * cos(thetaA / 2);
          tmpA.y = cos(phiA / 2) * sin(thetaA / 2);
          tmpA.z =-sin(phiA / 2) * sin(thetaA / 2);
          tmpB.w = cos(phiB / 2) * cos(thetaB / 2);  // Modified IMUB data
          tmpB.x = sin(phiB / 2) * cos(thetaB / 2);
          tmpB.y = cos(phiB / 2) * sin(thetaB / 2);
          tmpB.z =-sin(phiB / 2) * sin(thetaB / 2);
          // 2. Get the Configuration of Continuum Arm
          tmp.w = tmpB.w*tmpA.w + tmpB.x*tmpA.x + tmpB.y*tmpA.y + tmpB.z*tmpA.z;
          tmp.x = tmpB.w*tmpA.x - tmpB.x*tmpA.w - tmpB.y*tmpA.z + tmpB.z*tmpA.y;
          tmp.y = tmpB.w*tmpA.y + tmpB.x*tmpA.z - tmpB.y*tmpA.w - tmpB.z*tmpA.x;
          tmp.z = tmpB.w*tmpA.z - tmpB.x*tmpA.y + tmpB.y*tmpA.x - tmpB.z*tmpA.w;
          // 3. Adjust the Configuration of Continuum Arm
          q.w = sqrt(tmp.w * tmp.w + tmp.z * tmp.z);
          q.x = 1 / q.w * ( tmp.w * tmp.x + tmp.z * tmp.y);
          q.y = 1 / q.w * (-tmp.z * tmp.x + tmp.w * tmp.y);
          q.z = 0.0;
          imua.publish(&IMUA);
          //Serial.printf("q.[w,x,y,z]=[%.3f,%.3f,%.3f,%.3f]\n",q.w,q.x,q.y,q.z);
          //Serial.printf("q.[Phi,Theta]=[%.3f,%.3f]\n",atan2(2 * (q.w * q.x + q.y * q.z), 1 - 2 * (q.x * q.x + q.y * q.y)),  asin(2 * (q.w * q.y - q.x * q.z)));

          // 4. Dx Dy Parameters
          Gx.measure = ((q.y>0)?1:-1) * 2 * 40 * acos(q.w) / sqrt(1 + q.x * q.x / q.y / q.y);  // d = 40mm 
          Gy.measure = -q.x/q.y * Gx.measure; 
          Gx.measure = isnan(Gx.measure)?0.0:Gx.measure;
          Gy.measure = isnan(Gy.measure)?0.0:Gy.measure;
          Gx.measure -= deltaX;  // Calibration
          Gy.measure -= deltaY;
          //Serial.printf("[Gx.measure,Gy.measure]=[%.3f,%.3f]\n", Gx.measure, Gy.measure);
        }
      }
    }
    
  }
}

// fbCtrl loop
void fbCtrl_(void *pvParameters) {
  int Mx=0,My=0;
  while (1) {
    vTaskDelay(100);  // 1/0.100 = 10 Hz

    // Straight Flight (Outer Loop)
    if(fbCN==FB_SF){
      sf.err = sf.target - psi;
      sf.err_last = 0 + psi_*50;  // Here set yaw ratio times det_t psi_*(1/50) as diffential item
      Serial.printf("sf.[err,err']=[%.3f,%.3f]\n", sf.err, sf.err_last);
      Gy.target = (MAX(-stMax, MIN(stMax, sf.Kp*sf.err + sf.Kd*sf.err_last) ));
      //gondola(500, uint16_t(MAX(0, MIN(1000, My+500) )));
    }

    // Eular Spiral
    if(fbCN==FB_ES){
      Gy.target = (MAX(-50, MIN(50, Gy.target+slope) ));  // Linear Increase
    }

    // Square End Motion Trajectory
    if(fbCN==FB_SQ){
      if(!loopLemn && (esp_log_timestamp()-startTime)>2*(taLemn+tbLemn)){
         gondola(500,500);
         fbCN=FB_GD;isGD=GD_CLS;
      }
      float time_ = (esp_log_timestamp()-startTime)%int(2*(taLemn+tbLemn));
      if (time_ < taLemn) cntLemn = 0;
      else if(time_ < (taLemn+tbLemn)) cntLemn = 1;
      else if(time_ < (2*taLemn+tbLemn)) cntLemn = 2;
      else cntLemn = 3;
      switch(cntLemn){
      case 0:
         Gx.target = AxLemn*cos(6.283/(taLemn*2)*time_ - 3.1415);
         Gy.target = AyLemn;
         break;
      case 1:
         Gx.target = AxLemn;
         Gy.target = AyLemn*cos(6.283/(tbLemn*2)*(time_-taLemn));
         break;
      case 2:
         Gx.target = AxLemn*cos(6.283/(taLemn*2)*(time_-taLemn-tbLemn));
         Gy.target =-AyLemn;
         break;
      case 3:
         Gx.target =-AxLemn;
         Gy.target = AyLemn*cos(6.283/(tbLemn*2)*(time_-2*taLemn-tbLemn) - 3.1415);
         break;
      }
      //Serial.printf("%.3f,%.3f\n", Gx.target, Gy.target);
    }

    // Triangular End Motion Trajectory
    if(fbCN==FB_TR){
      if(!loopLemn && (esp_log_timestamp()-startTime)>(taLemn+2*tbLemn)){
         gondola(500,500);
         fbCN=FB_GD;isGD=GD_CLS;
      }
      float time_ = (esp_log_timestamp()-startTime)%int(taLemn+2*tbLemn);
      if (time_ < tbLemn) cntLemn = 0;
      else if(time_ < (tbLemn + taLemn)) cntLemn = 1;
      else cntLemn = 2;
      switch(cntLemn){
      case 0:
         Gx.target = AxLemn*sin(6.283/(tbLemn*4)*time_ - 3.1415);
         Gy.target = AyLemn*sin(6.283/(tbLemn*4)*time_ - 3.1415);
         break;
      case 1:
         Gx.target = AxLemn*cos(6.283/(taLemn*2)*(time_-tbLemn)-3.1415);
         Gy.target =-AyLemn;
         break;
      case 2:
         Gx.target = AxLemn*cos(6.283/(tbLemn*4)*(time_-tbLemn-taLemn));
         Gy.target =-AyLemn*cos(6.283/(tbLemn*4)*(time_-tbLemn-taLemn));
         break;
      }
      //Serial.printf("%.3f,%.3f\n", Gx.target, Gy.target);
    }
    
    // Gondola Distance PID Ctrl
    if(isGD){
      // PID Gondola X
      Gx.err = Gx.target-Gx.measure;
      Gx.integral = MAX(-500, MIN(500, Gx.integral+Gx.err) );
      Mx = Gx.Kp*Gx.err + Gx.Ki*Gx.integral + Gx.Kd*(Gx.err-Gx.err_last);
      Mx = ((abs(Mx)<6) or    !(isGD%2))?0:Mx;
      Gx.err_last = Gx.err;

      // PID Gondola Y
      Gy.err = Gy.target-Gy.measure;
      Gy.integral = MAX(-500, MIN(500, Gy.integral+Gy.err) );
      My = Gy.Kp*Gy.err + Gy.Ki*Gy.integral + Gy.Kd*(Gy.err-Gy.err_last);
      My = ((abs(My)<6) or !(isGD>>1%2))?0:My;
      Gy.err_last = Gy.err;

      gondola(uint16_t(MAX(0, MIN(1000, Mx+500) )), uint16_t(MAX(0, MIN(1000, My+500) )));
      //Serial.printf("[Dx,Dy]=[%.3f,%.3f], [Mx,My,DY]=[%d,%d,%d]\n", Gx.measure, Gy.measure, Mx, My, Gy.target);
    }
  }
}

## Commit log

2024-06-18 Update PCB
    [PCB_RGBlimp-Q.pcbdoc, PCB_RGBlimp-Q.schdoc, PCB_RGBlimp-Q_Subplate.pcbdoc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]
2024-06-18 Update BOM
    [BOM_RGBlimp-Q.csv]
